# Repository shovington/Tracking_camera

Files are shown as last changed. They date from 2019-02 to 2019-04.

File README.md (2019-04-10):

# Tracking camera

## Overview

Tracking camera : This package controls a 3 axis 3D printed gimbal using computer vision to track human faces and/or body. The gimbal can also be controlled manually via an rqt interface. Everything works in a ROS environnement. In this package, you can find all the mechanical parts needed to build our project as well as all the code to make it work. 

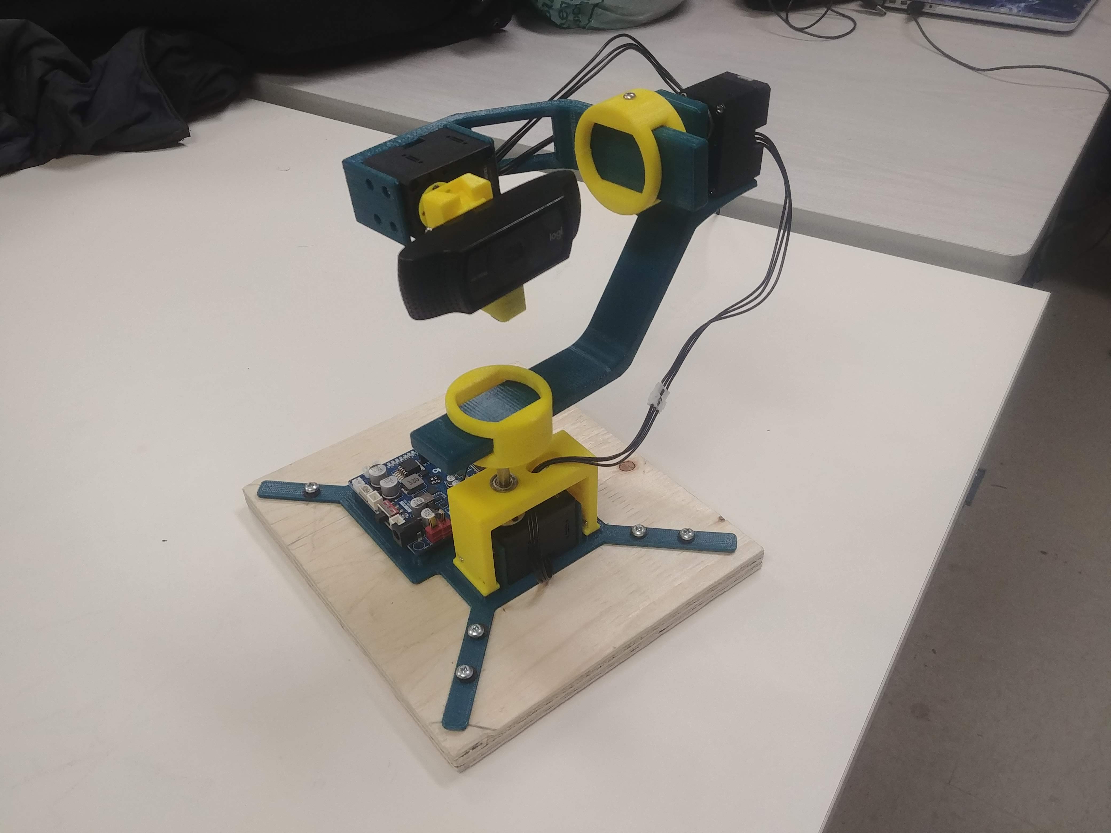
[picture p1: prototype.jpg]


## Install

### Mechanical assembly
To assemble the mechanical parts you'll have to 3D print a few parts and buy some others. For complete instruction about how to procede, follow [this guide](https://github.com/shovington/Tracking_camera/blob/master/Mechanical/Assembly%20Guide.pdf)

### OpenCR setup

To control the motors with ROS you’ll need to put the OpenCR board into a usb to dynamixel bridge. 

First, change your port permissions by typing this command line:

```bash
[user@machine ~]$ sudo usermod -a -G dialout <user>
```
Note that you have to logout/login to make the change available
.
Then follow the instructions [here](http://emanual.robotis.com/docs/en/parts/controller/opencr10/#arduino-ide) to make your board visible on Arduino IDE. You only have to follow the steps from 4. 1. Install on Linux to 4. 1. 5. 3. Port Setting

Now you can upload the following code File -> Examples -> OpenCR -> 10.Etc -> usb_to_dxl

### Software

For this project, you will need a computer or Jetson Xavier as well as an OpenCR. First of all, you need to have Ubuntu 18.04 installed on your computer as well as ROS Melodic. Here are the installation steps :
 
http://wiki.ros.org/melodic/Installation/Ubuntu

Dependencies:

1. darknet_ros
3. dynamixel_workbench
2. usb_cam

```bash
sudo apt-get install ros-melodic-dynamixel-workbench
sudo apt-get install ros-melodic-usb-cam
```
darknet_ros is not yet supported on Melodic, so you will need to build it from the source.

https://github.com/leggedrobotics/darknet_ros

After cloning our repository, build in your catkin workspace :

```bash
git clone https://github.com/shovington/Tracking_camera.git
catkin_make
```

## Usage

Once everything is installed, run our project with

	roslaunch tracking_camera full.launch

To run only manual mode

	roslaunch tracking_camera manual.launch

Here's what our user interface looks like when launched.

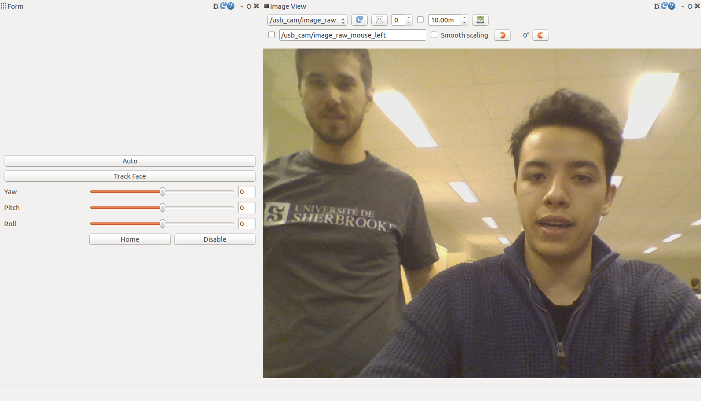
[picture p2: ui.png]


## Config files

Darknet config

* **darknet.yaml**     

Contains the camera configuration for darknet and which image topic to subscribe to.

Motors config

* **config_motors.yaml**     

Contains the motors configuration : IDs, names, etc.

Yolo config

* **yolov3.yaml**     

Contains yolo configuration : Accuracy threshold, classes to track.

## Nodes

### tracking_cam_plugin node

This is the only node in the package. It is a rqt plugin. You can control the gimbal manually using the UI sliders. It also subscribes to darknet and controls the gimbal to track faces when it is put in auto mode.

##### Subscribed Topics

* **`/dynamixel_workbench/dynamixel_state `** ([dynamixel_workbench_msgs/DynamixelStateList])

	Motors live states
	
* **`/darknet_ros/bounding_boxes `** ([sensor_msgs/NatSatFix])

	Position and dimension of detected objects

## Run automated tests

Enter this line in terminal:
```bash
rostest tracking_camera test_test.test 

```

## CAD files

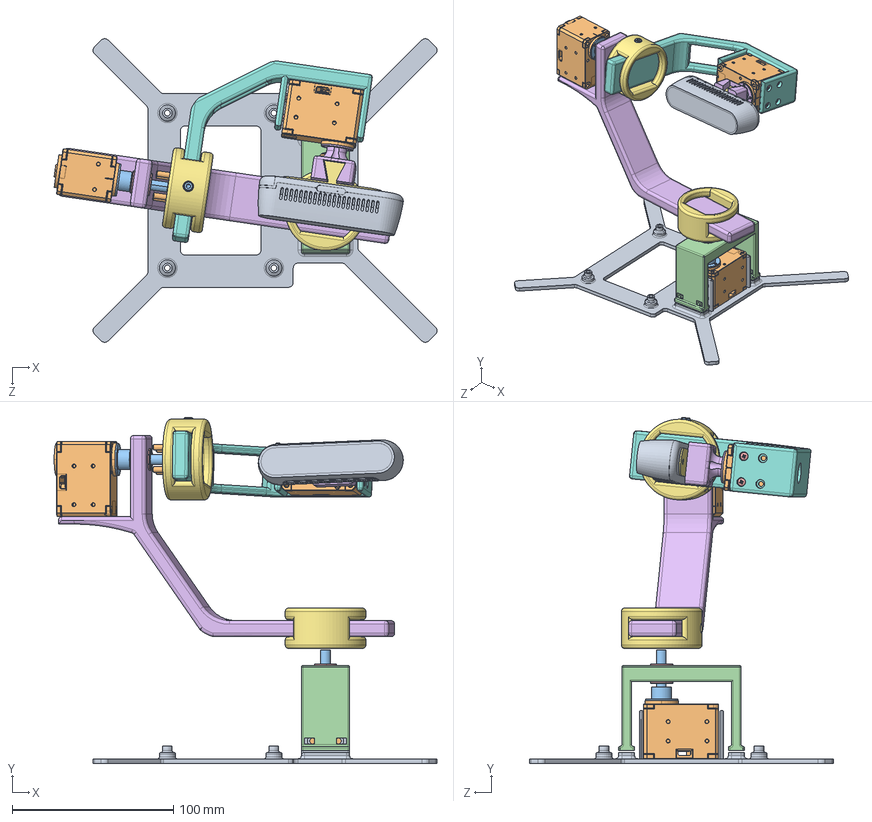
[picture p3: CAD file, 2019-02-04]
Mechanical/Custom parts/Assem_full.SLDASM
237.4 x 214.6 x 188.2 mm
01_BASE
dynamixel_motor x 3
03_COUPLING x 2
02_BRIDGE
bearing x 4
05_LONG_ARM
04_ARM_FIX x 2
06_SHORT_ARM
IntelRealsense_D435_Multibody
socket head cap screw_ai x 4
socket head cap screw_am
hex nut style 1_am
pan cross head_am x 10
07_CAM_MOUNT
09_REALSENSE_MOUNT

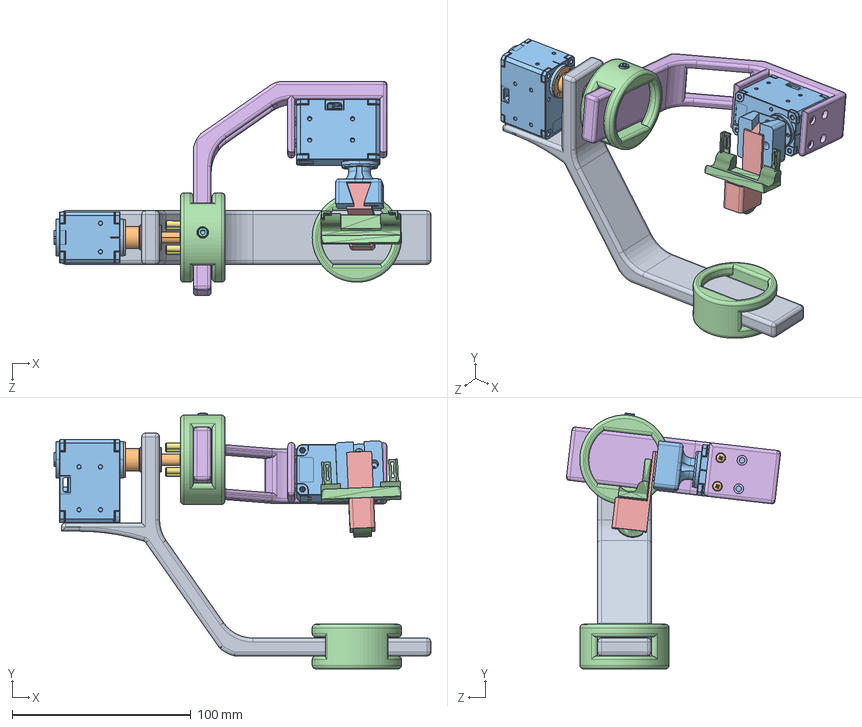
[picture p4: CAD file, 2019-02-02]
Mechanical/Custom parts/Assem_c920.SLDASM
211.0 x 143.2 x 119.8 mm
05_LONG_ARM
03_COUPLING
dynamixel_motor x 2
04_ARM_FIX x 2
bearing x 2
06_SHORT_ARM
socket head cap screw_ai x 4
socket head cap screw_am
hex nut style 1_am
pan cross head_am x 10
07_CAM_MOUNT
C920_Mount
08_C920_MOUNT

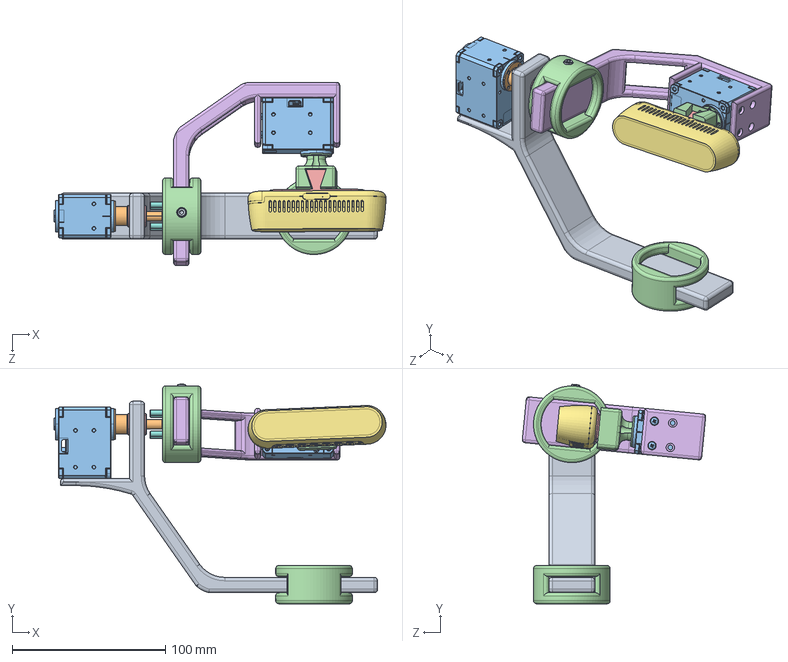
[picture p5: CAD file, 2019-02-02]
Mechanical/Custom parts/Assem_realsense.SLDASM
216.4 x 143.2 x 119.5 mm
05_LONG_ARM
03_COUPLING
dynamixel_motor x 2
04_ARM_FIX x 2
bearing x 2
06_SHORT_ARM
IntelRealsense_D435_Multibody
socket head cap screw_ai x 4
socket head cap screw_am
hex nut style 1_am
pan cross head_am x 10
07_CAM_MOUNT
09_REALSENSE_MOUNT

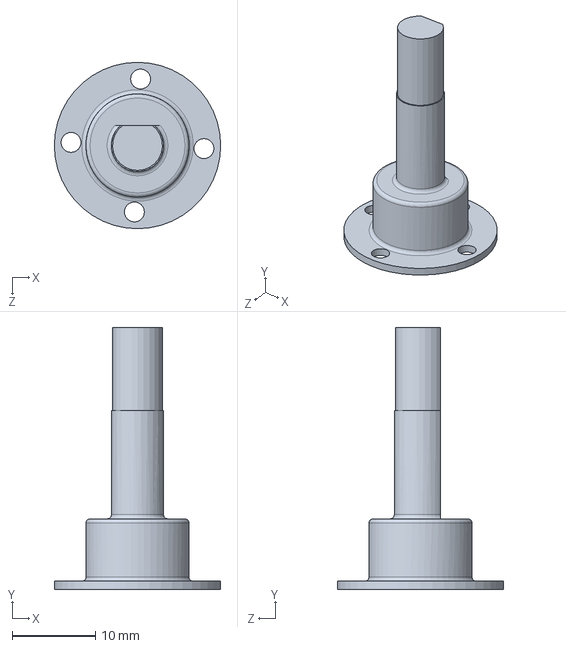
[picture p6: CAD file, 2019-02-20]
Mechanical/Custom parts/03_COUPLING.SLDPRT
20.0 x 31.5 x 20.0 mm

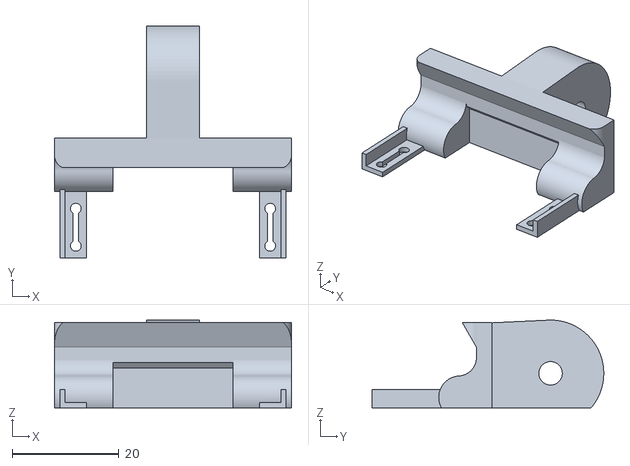
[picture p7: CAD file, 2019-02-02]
Mechanical/stl/C920_Mount.stl
44.5 x 43.5 x 16.5

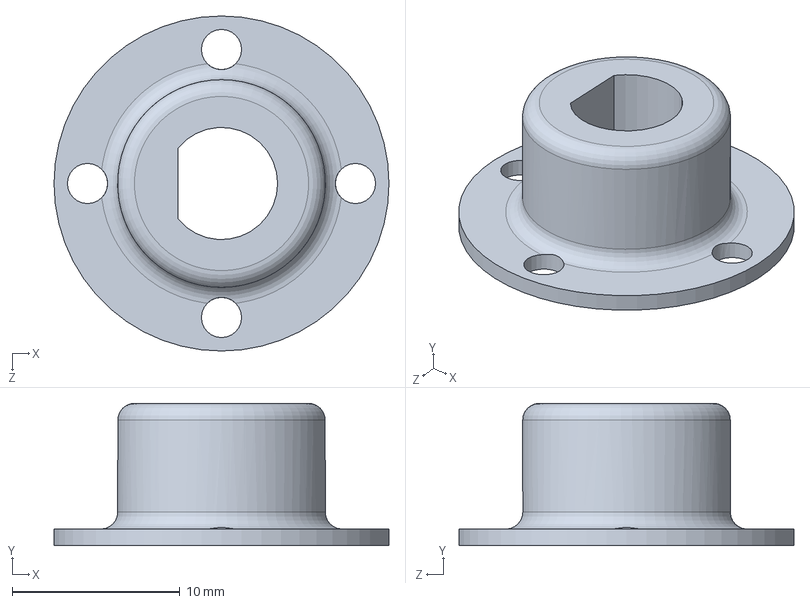
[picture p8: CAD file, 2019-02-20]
Mechanical/Custom parts/11_EMPTY_COUPLING.SLDPRT
20.0 x 8.50 x 20.0 mm

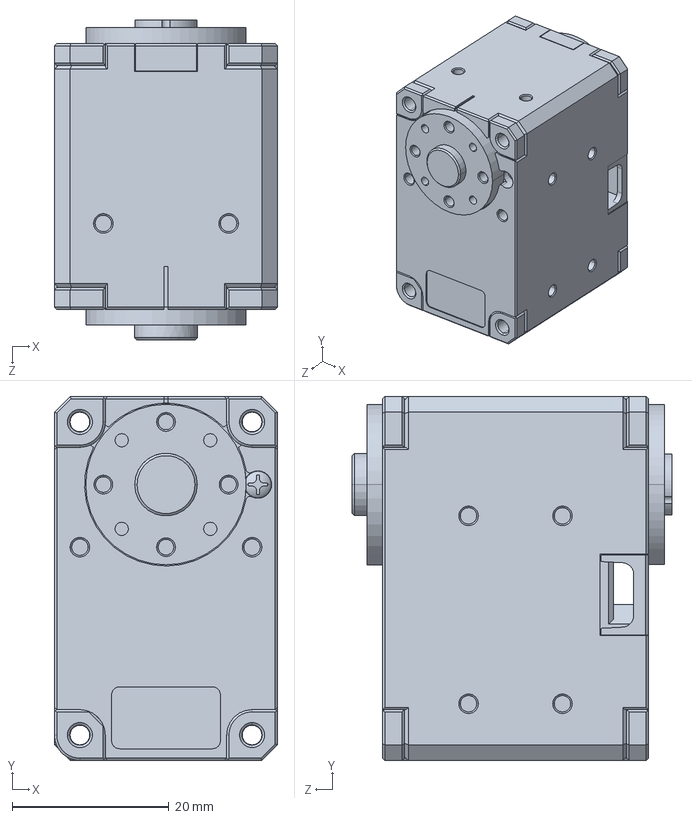
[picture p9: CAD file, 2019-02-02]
Mechanical/other/dynamixel_motor.SLDPRT
28.5 x 46.5 x 40.9 mm

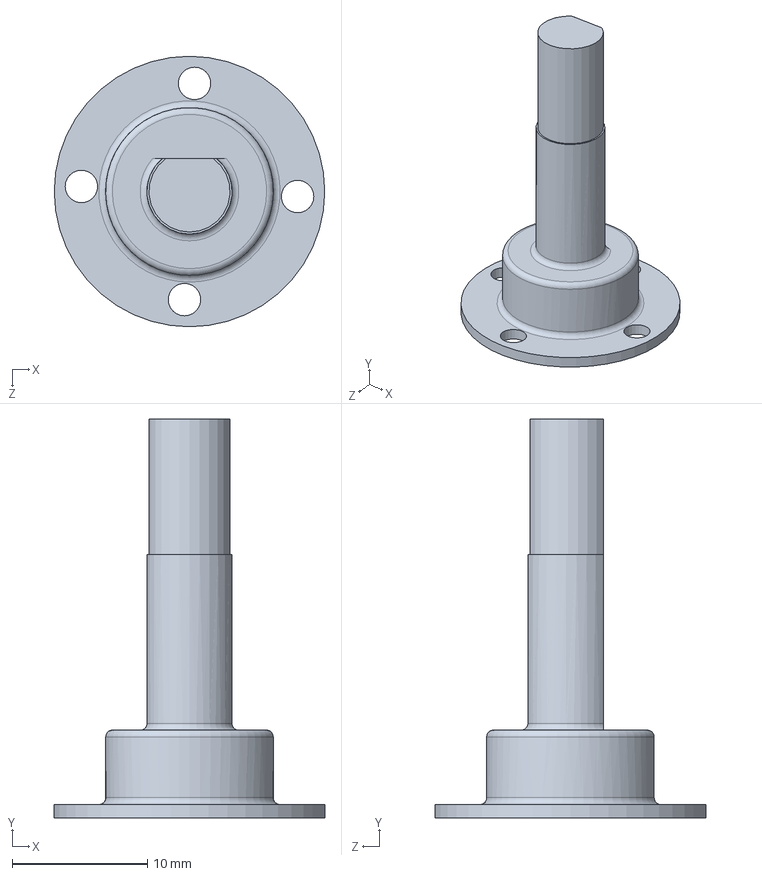
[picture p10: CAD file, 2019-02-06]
Mechanical/Custom parts/10_COUPLING.SLDPRT
20.0 x 29.5 x 20.0 mm

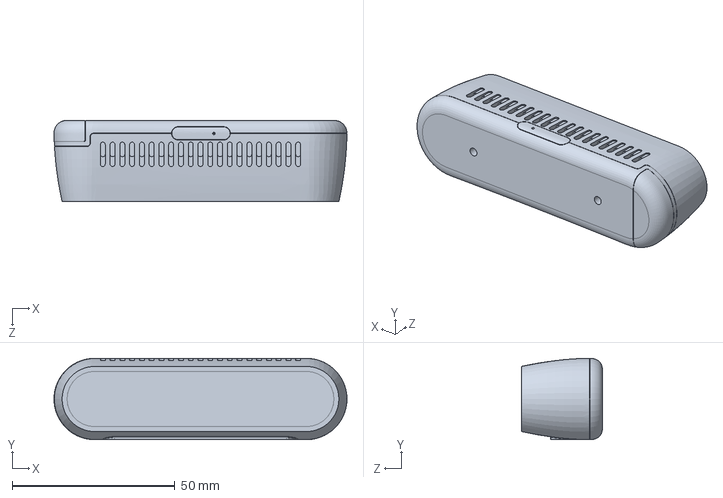
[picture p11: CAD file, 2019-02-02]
Mechanical/other/IntelRealsense_D435_Multibody.SLDPRT
90.0 x 25.0 x 25.0 mm

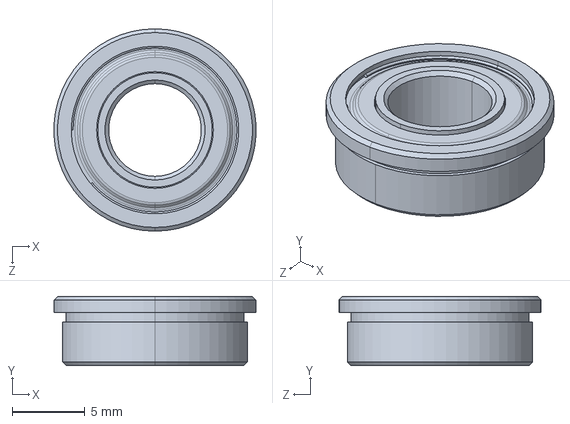
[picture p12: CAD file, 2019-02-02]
Mechanical/other/bearing.SLDPRT
13.8 x 4.75 x 13.9 mm

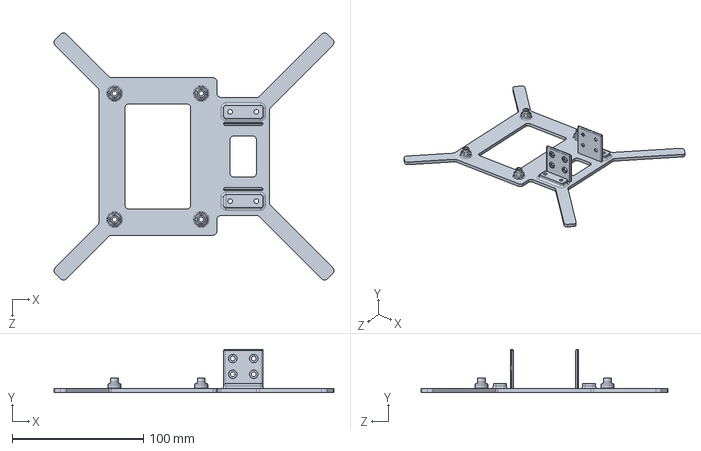
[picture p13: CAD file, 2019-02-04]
Mechanical/Custom parts/01_BASE.SLDPRT
213.2 x 33.0 x 188.2 mm

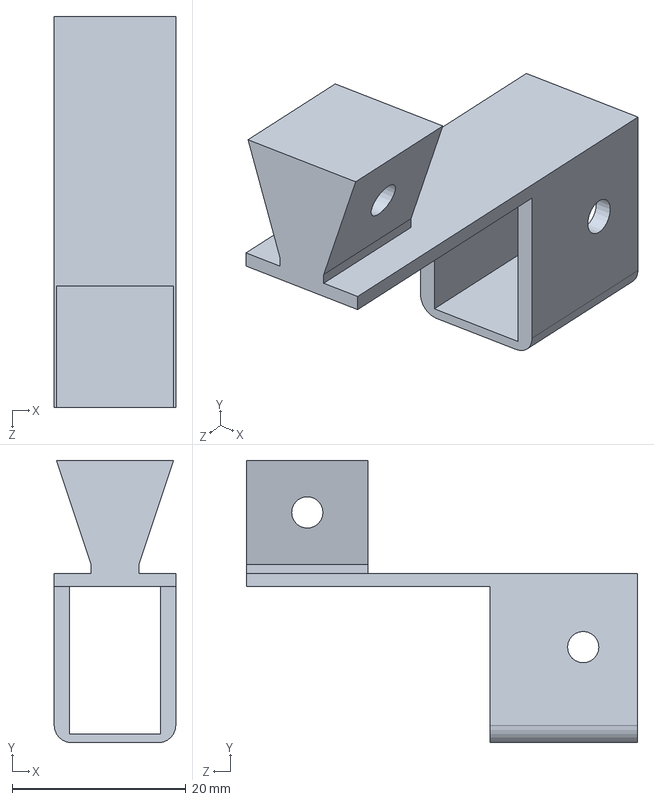
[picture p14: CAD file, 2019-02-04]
Mechanical/Custom parts/08_C920_MOUNT.SLDPRT
14.0 x 32.5 x 45.0 mm

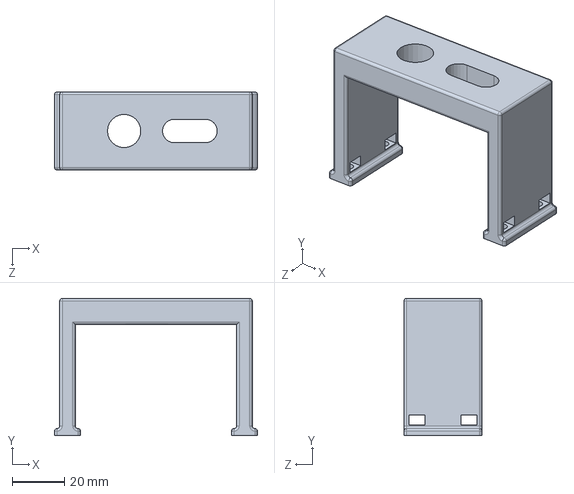
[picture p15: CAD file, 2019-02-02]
Mechanical/Custom parts/02_BRIDGE.SLDPRT
78.0 x 52.8 x 30.0 mm

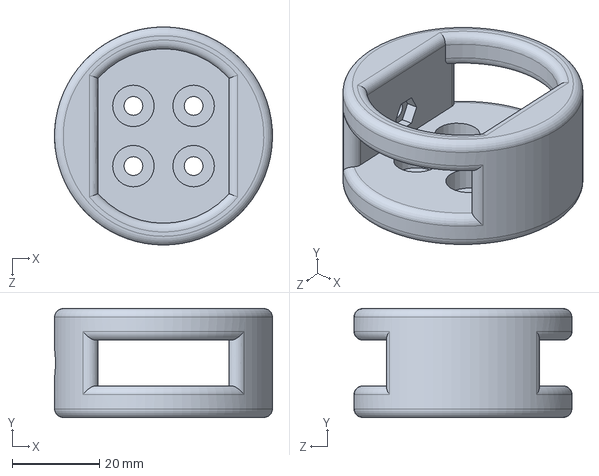
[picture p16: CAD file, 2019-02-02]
Mechanical/Custom parts/04_ARM_FIX.SLDPRT
50.0 x 25.0 x 50.0 mm

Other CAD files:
Mechanical/other/C920_Mount.SLDPRT
Mechanical/Custom parts/07_CAM_MOUNT.SLDPRT
Mechanical/Custom parts/09_REALSENSE_MOUNT.SLDPRT
Mechanical/Custom parts/05_LONG_ARM.SLDPRT
Mechanical/Custom parts/06_SHORT_ARM.SLDPRT
Mechanical/other/545548.STEP.SLDPRT

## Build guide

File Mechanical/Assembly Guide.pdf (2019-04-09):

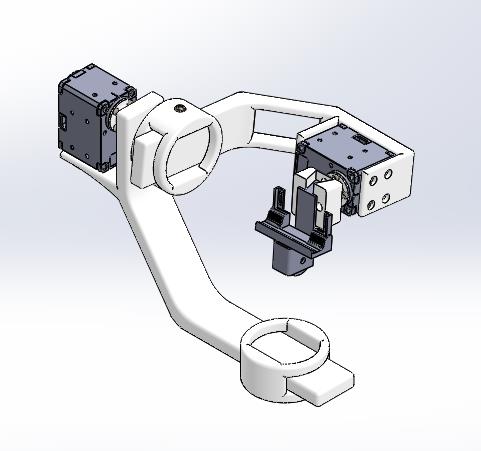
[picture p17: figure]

# ASSEMBLY GUIDE

# Bill of material (BOM)

2 Dynamixel motor XL430-W250-T
1 Dynamixel motor XM430-W350-T 1 Dynamixel controller openCR 1.0 1 Dynamixel cable V3P 240 mm 2 Dynamixel cable V3P 180mm
1 Dynamixel cable V3P 100mm
1 F to F adapter
1 12V 7.5A power supply for motor and openCR 1 6mm Set Screw D-Hubs
¼” Bore Set Screw
1 01_BASE
1 02_BRIDGE
1 03_COUPLING
2 04_ARM_FIX
1 05_LONG_ARM
1 06_SHORT_ARM
1 07_CAM_MOUNT
1 08_C920_MOUNT
1 09_REALSENSE_MOUNT
1 10_COUPLING
1 11_EMPTY_COUPLING

# PART 1

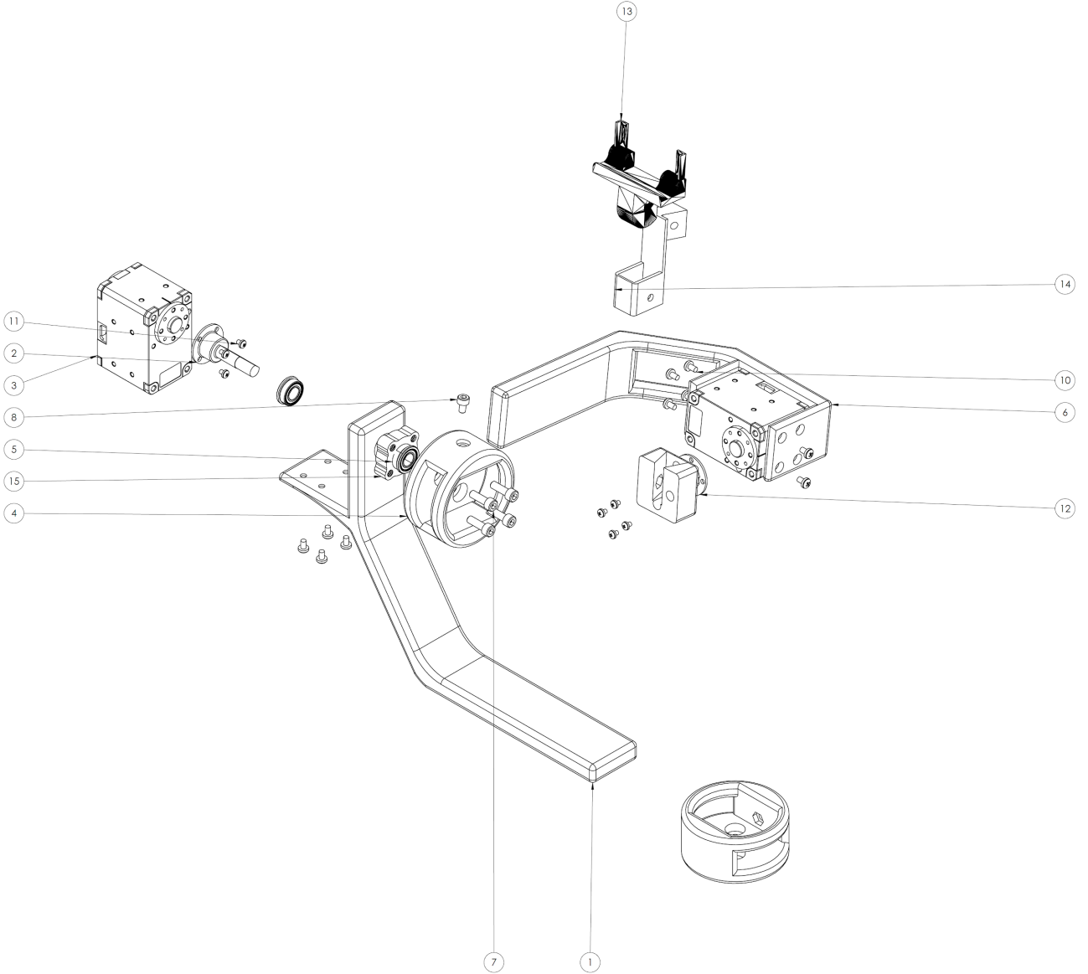
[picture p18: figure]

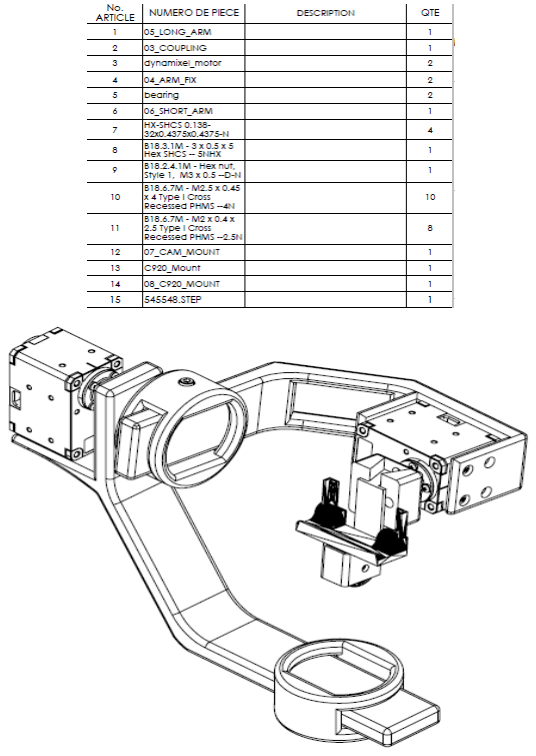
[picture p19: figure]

# Instructions

1. Fix the 535198 bearing on the outer side of the 05_LONG_ARM’s smaller part

2. Fix the 545548 bearing on the inner side of the 05_LONG_ARM’s smaller part
3. Fix the 03_COUPLING to the Dynamixel motor XL430-W250-T using the M2 x 0.4 x 2.5 screw
4. Pass the 03_COUPLING through the bearings
5. Fix the Dynamixel motor XL430-W250-T to the 05_ LONG_ARM using the M2.5 x 0.45 x 4 screw
6. Fix a 04_ARM_FIX on the 545548 bearing inner bearing using the HX-SHCS 0.138-32x0.4375x0.4375-N screw
7. Fix the Dynamixel motor XL430-W250-T on the 06_SHORT_ARM using the M2.5 x 0.45 x 4 screw
8. Fix the 07_CAM_MOUNT on the previous Dynamixel motor using the M2 x 0.4 x 2.5 screw
9. Slide the 08_C920_MOUNT in the 07_CAM_MOUNT
10. Slide the 06_SHORT_ARM in the 04_ARM_FIX and fix a M-3x0.5x5 Hex SHCS screw on the top until the friction keeps the 06_SHORT_ARM in place
11. Slide a 04_ARM_FIX on the larger part 05_LONG_ARM until the holes are aligned

# PART 2

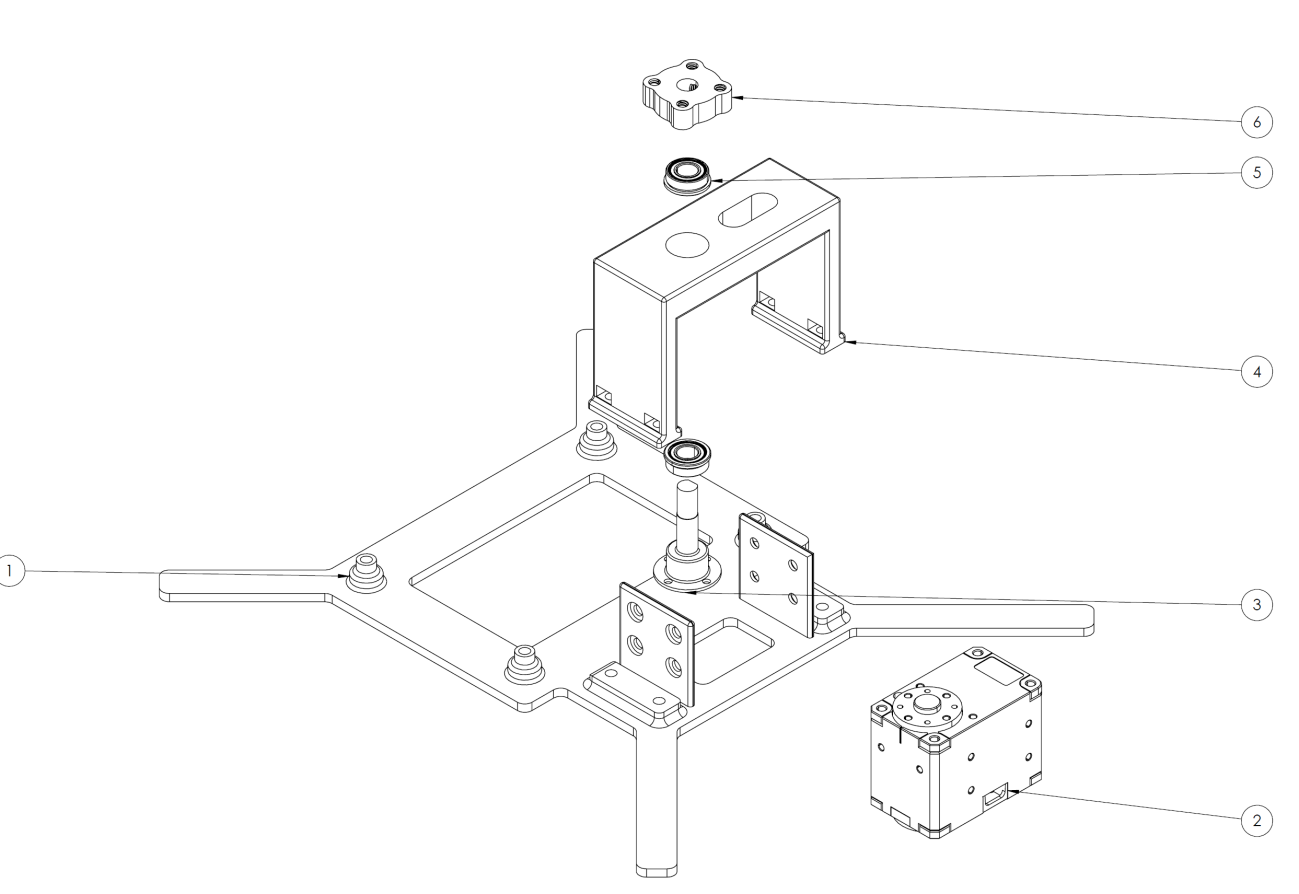
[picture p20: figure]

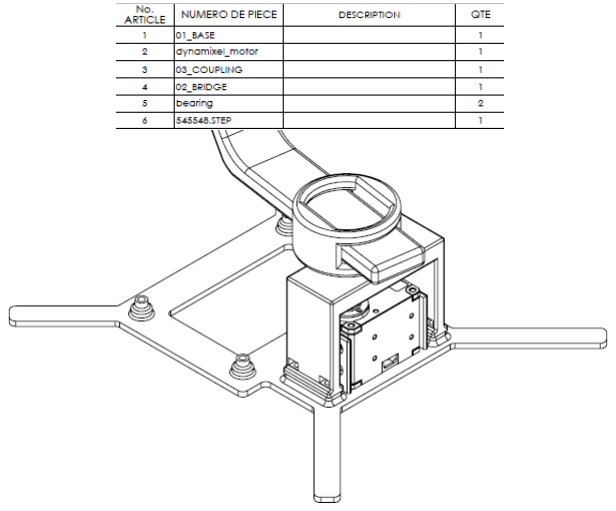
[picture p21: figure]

# Instructions

1. Fix the Dynamixel motor to the 01_BASE using the M2.5 x 0.45 x 4 screw
2. Fix the 03_COUPLING to the Dynamixel motor XL430-W250-T using the M2 x 0.4 x 2.5 screw
3. Fix the 535198 bearing at the extremity of the 03_COUPLING
4. Fix the 535198 bearing on the outer side of the 02_BRIDGE
5. Fix the 545548 bearing on the outer side of the 02_BRIDGE
6. Fix the 02_BRIDGE on the 01_BASE using the M2.5 x 0.45 x 4 screw

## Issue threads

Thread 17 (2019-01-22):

Control motors from keyboard

shovington, 2019-01-22:
child of #7

shovington, 2019-01-29:
We can control motor with arduino IDE but now we have to control it with ROS

Closed 2019-01-29.

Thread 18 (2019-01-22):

Chose between Raspberry PI and Jetson

shovington, 2019-01-22:
child of #4

shovington, 2019-01-23:
We chose the Jetson and we will continue developping on the PC until the Jetson is availible.

Closed 2019-01-23.

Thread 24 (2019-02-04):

Fix first prototype CAD and assemble gimbal

simonchamorro, 2019-02-04:
Child of #6

Closed 2019-02-05.

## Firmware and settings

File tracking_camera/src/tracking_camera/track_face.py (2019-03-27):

#!/usr/bin/env python

import numpy as np
import rospy
from rospkg import RosPack
from std_msgs.msg import String, Int32
from darknet_ros_msgs.msg import BoundingBoxes

class TrackFace():
    def __init__(self):
	pass

    def box_offset(self, box): #We take the first index only which is the one who has the most probability

        center_image=list()
        center_image=[320,240]

        center_box=list()
        command=list()

        for i in range(len(box.bounding_boxes)):

            if box.bounding_boxes[i].Class=="person":

                center_box.append((box.bounding_boxes[i].xmin+box.bounding_boxes[i].xmax)/2)
                center_box.append((box.bounding_boxes[i].ymin+box.bounding_boxes[i].ymax/3))

                command.append(center_box[0]-center_image[0])
                command.append(center_box[1]-center_image[1])

                break

        return command


if __name__ == "__main__":

    print("Face tracking started")
    rospy.init_node('track_face')

    try:
        tracking = TrackPerson()
    except rospy.ROSInterruptException:
        pass

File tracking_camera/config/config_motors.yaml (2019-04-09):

# You can find control table of Dynamixel on emanual (http://emanual.robotis.com/#control-table)
# Control table item has to be set Camel_Case and not included whitespace
# You are supposed to set at least Dynamixel ID
# This example is compatible with Dynamixel using protocol 2.0
yaw:
  ID: 1
  Return_Delay_Time: 0
  Operating_Mode: 3
  Profile_Acceleration: 0
  Profile_Velocity: 0
  Min_Position_Limit: 1194
  Max_Position_Limit: 3242

pitch:
  ID: 2
  Return_Delay_Time: 0
  Operating_Mode: 3
  Profile_Acceleration: 0
  Profile_Velocity: 0
  Max_Position_Limit: 3594
  Min_Position_Limit: 1546

roll:
  ID: 3
  Return_Delay_Time: 0
  Operating_Mode: 3
  Profile_Acceleration: 0
  Profile_Velocity: 0
  Min_Position_Limit: 1024
  Max_Position_Limit: 3072

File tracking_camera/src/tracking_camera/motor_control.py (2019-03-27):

#!/usr/bin/env python

import rospy
from std_msgs.msg import Float32, Bool, Int32, Int32MultiArray
from sensor_msgs.msg import Joy
from dynamixel_workbench_msgs.srv import *
from dynamixel_workbench_msgs.msg import *
from constants import *
from timeit import default_timer as timer


class MotorControl():
    def __init__(self):
        self.motors = 0

        try:
            rospy.wait_for_service('/dynamixel_workbench/dynamixel_command', 0.1)
            self.motor_proxy = rospy.ServiceProxy('/dynamixel_workbench/dynamixel_command', DynamixelCommand)
            self.motors = 1
        except:
            self.motors = 0
            print("WAITING FOR DYNAMIXEL MOTORS")
            self.timer = rospy.Timer(rospy.Duration(2), self.connect)

        # Set max speed
        self.call_motor_cmd(1, "Position_P_Gain", 300)
        self.call_motor_cmd(2, "Position_P_Gain", 350)
        self.call_motor_cmd(3, "Position_P_Gain", 400)
        
        self.angles = [0, 0, 0]
        self.limits = [YAW, PITCH, ROLL]

    def connect(self, event):
        try:
            rospy.wait_for_service('/dynamixel_workbench/dynamixel_command', 0.1)
            self.motor_proxy = rospy.ServiceProxy('/dynamixel_workbench/dynamixel_command', DynamixelCommand)
            self.timer.shutdown()
            self.motors = 1
            print("MOTORS FOUND")
        except:
            self.motors = 0
            print("WAITING FOR DYNAMIXEL MOTORS")

    def update_motors(self, angles):
        self.angles = angles

    # Enable motors
    def enable_motors(self, enable):
        if self.motors == 0:
            return

        self.call_motor_cmd(1, "Torque_Enable", enable)
        self.call_motor_cmd(2, "Torque_Enable", enable)
        self.call_motor_cmd(3, "Torque_Enable", enable)

    def go_home(self):
        if self.motors == 0:
            return

        self.call_motor_cmd(1, "Goal_Position", YAW_HOME)  
        self.call_motor_cmd(2, "Goal_Position", PITCH_HOME)  
        self.call_motor_cmd(3, "Goal_Position", ROLL_HOME)

    def move_axis(self, axis, value, limits):
        if self.motors == 0:
            return

        self.call_motor_cmd(axis, "Goal_Position", value*2048/(limits[1]-limits[0]) + HOME[axis-1])
        
    def move_relative(self, axis, value):
        if self.motors == 0:
            return

        if self.limits[axis-1][1] < value+ self.angles[axis-1] or value+ self.angles[axis-1] < self.limits[axis-1][0]:
            print("Out of range")
            pass
        else:
            self.call_motor_cmd(axis, "Goal_Position", value + self.angles[axis-1])

    # Call motor service
    def call_motor_cmd(self, id, cmd, val):
        if self.motors == 0:
            return

        try:
            move_motor = rospy.ServiceProxy('/dynamixel_workbench/dynamixel_command', DynamixelCommand)            
            request = DynamixelCommandRequest()
            request.id = id
            request.addr_name = cmd
            request.value = val
            response = self.motor_proxy(request)
            
        except rospy.ServiceException, e:
            print "Service call failed: %s"%e
            

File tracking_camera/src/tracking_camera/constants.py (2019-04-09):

MANUAL = 0
AUTO = 1

YAW_HOME = 2218
PITCH_HOME = 2570
ROLL_HOME = 2048
HOME = [YAW_HOME, PITCH_HOME, ROLL_HOME]

RANGE = 2048

YAW = [YAW_HOME-(RANGE/2), YAW_HOME+(RANGE/2)]
PITCH = [PITCH_HOME-(RANGE/2), PITCH_HOME+(RANGE/2)]
ROLL = [ROLL_HOME-(RANGE/2), ROLL_HOME+(RANGE/2)]

STEP = RANGE//180

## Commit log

2019-02-02 first prototype 3D model
    [01_BASE.SLDPRT, 02_BRIDGE.SLDPRT, 03_COUPLING.SLDPRT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]
2019-02-02 added hole for wires in the birdge
    [02_BRIDGE.SLDPRT, adapter.STL, base.STL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]
2019-02-04 fixed holes in logitech mount
    [08_C920_MOUNT.SLDPRT]
2019-02-04 edited coupling for bigger motor
    [01_BASE.SLDPRT, 10_COUPLING.SLDPRT, Assem_full.SLDASM]
2019-02-06 refactored track face node by creating a class
2019-02-06 fixed coupling width
    [03_COUPLING.SLDPRT, 10_COUPLING.SLDPRT]
2019-02-06 Bug fixed, processing slow
    [track_face.py]
2019-02-07 added home position and motors disable
2019-02-12 added buttons callbacks
2019-02-15 manual control works with interface but doesnt show current pos
2019-02-20 manual control works
    [config_motors.yaml]
2019-02-20 gui messages go directly to motor node for faster reaction time
2019-02-20 fixed bugs, deleted tracking_camera_gui
    [tracking_cam_plugin.py]
2019-02-20 created empty coupling for metal shaft
    [11_EMPTY_COUPLING.SLDPRT]
2019-02-20 added holes to coupling
    [03_COUPLING.SLDPRT, 11_EMPTY_COUPLING.SLDPRT]
2019-03-13 auto mode face track
2019-03-27 Smoother control, ui now in deg, code is independent from motors
    [config_motors.yaml]
2019-04-09 Add assembly guide and reorganize mechanical folder
    [01_BASE.SLDPRT, 02_BRIDGE.SLDPRT, 03_COUPLING.SLDPRT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]
2019-04-09 changed motors ids, added launch file
    [config_motors.yaml]
